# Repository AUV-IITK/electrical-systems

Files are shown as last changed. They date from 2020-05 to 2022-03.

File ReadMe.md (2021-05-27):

**This is the repository for AUV-IITK Electrical subsytem**

Implementing new electrical design with multiple 2layer PCB and more compatible connectors making the electronics modular.
Introducing :
- Power Board for Power Management and routing with fault detection and indicators.
- custom Microcontroller Board
- ESC Breakout boards

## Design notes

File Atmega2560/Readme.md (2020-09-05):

**This is the repository for ATMEGA 2560**

The MicrocontrollerPCB section contains the scematic and the PCB layout done in KICAD and would be updated from time to time.

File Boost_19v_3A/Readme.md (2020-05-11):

# Boost Converter for the NUC

 The simulation has been run on TINA-TI Spice software. Download from here [Link](http://www.ti.com/tool/TINA-TI).

 Results of a simulation on the [Webench](https://webench.ti.com/power-designer/) have been placed in the in the simulation output folder. 

 To run simulation download the schematic and open with TINA-TI.

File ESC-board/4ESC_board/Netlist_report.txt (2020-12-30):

Info: Checking netlist symbol footprint “C1:/5FEA16F4:molex:molex_supersabre_1x2_172043-0201”.

Info: Checking netlist symbol footprint “C2:/5FEA11BD:molex:Molex_Microfit_1x5_436500500”.

Info: Checking netlist symbol footprint “C3:/5FEA0F57:molex:Molex_microfit_2x6_444281201”.

Info: Checking netlist symbol footprint “D1:/5FEA1FA2:Diode_SMD:D_1206_3216Metric_Pad1.42x1.75mm_HandSolder”.

Info: Checking netlist symbol footprint “R1:/5FEA2178:Resistor_SMD:R_1206_3216Metric_Pad1.42x1.75mm_HandSolder”.

Info: Checking netlist symbol footprint “U1:/5FEA0291:ESC:ESC_footprint”.

Info: Checking netlist symbol footprint “U2:/5FEA037F:ESC:ESC_footprint”.

Info: Checking netlist symbol footprint “U3:/5FEA0417:ESC:ESC_footprint”.

Info: Checking netlist symbol footprint “U4:/5FEA04B8:ESC:ESC_footprint”.

Adding new symbol “C1:/5FEA16F4” footprint “molex:molex_supersabre_1x2_172043-0201”.

Changing footprint “C1:/5FEA16F4” pad “2” net name from “” to “/GND”.

Changing footprint “C1:/5FEA16F4” pad “1” net name from “” to “/VIN”.

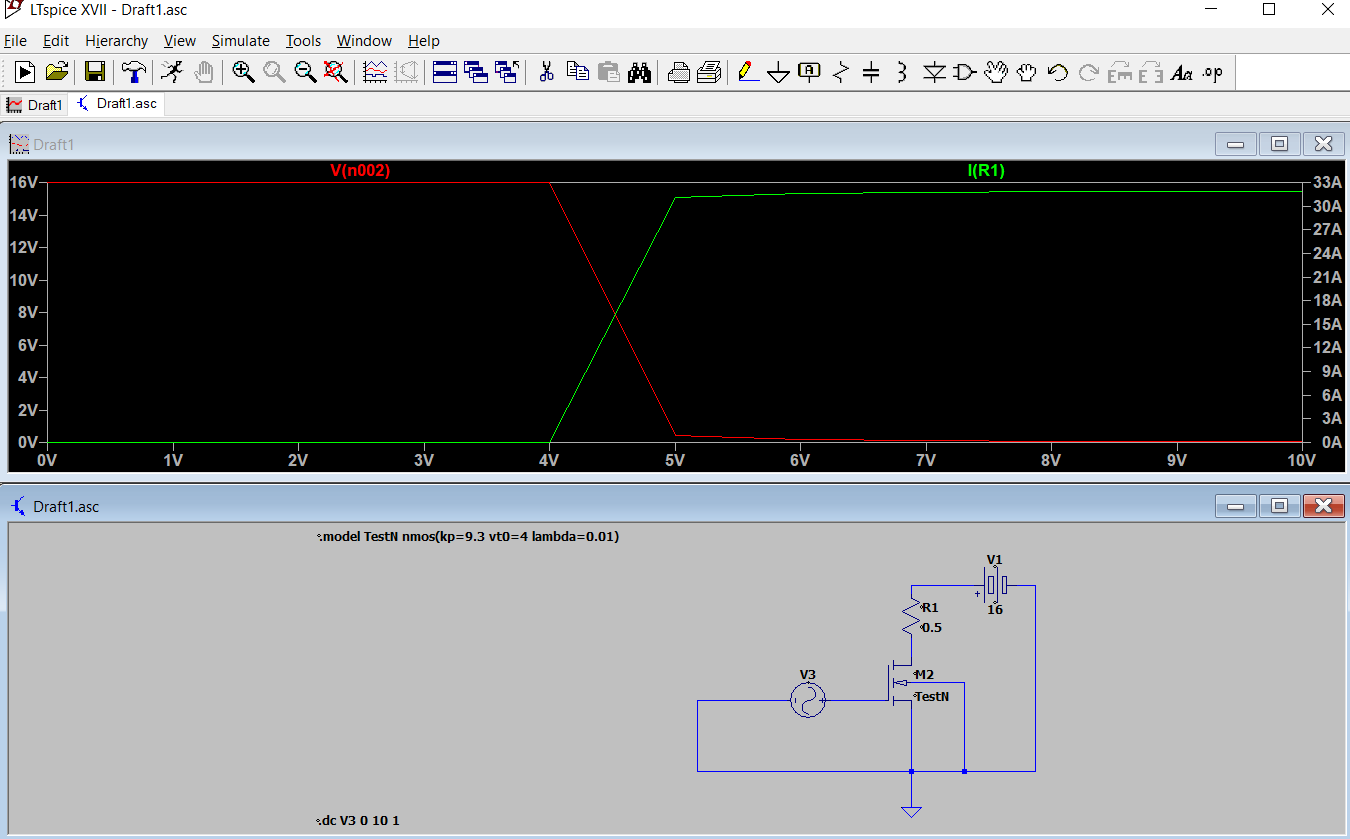
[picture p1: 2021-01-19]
Kill_switch_board/Mosfet/Simulation.png

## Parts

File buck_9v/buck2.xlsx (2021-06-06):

Reference | Value | Price | Mouser Price/Stock | Description | Height | Manufacturer_Name | Manufacturer_Part_Number | Mouser Part Number | Availability | MF | MP | Package | Datasheet
Cvcc1 | 1uF,1mOhm | 12.69 | https://www.mouser.in/ProductDetail/Taiyo-Yuden/TMK212B7105KG-T |  |  |  |  |  |  |  |  |  | ~
Ccomp1 | 18nF,0Ohm | 128.4 | https://www.mouser.in/ProductDetail/KEMET/C1812C183J5GACTU |  |  |  |  |  |  |  |  |  | ~
Cbst1 | 100nF,1mOhm | 7.47 | https://www.mouser.in/ProductDetail/Murata-Electronics/GRM155R71C104KA88D?qs=8YPuuxuUzMJKePo9sU3A2g%3D%3D |  |  |  |  |  |  |  |  |  | ~
Rcomp1 | 2.43kOhm | 7.47 | https://www.mouser.in/ProductDetail/Vishay-Dale/CRCW04022K43FKED?qs=hD42E%2F8yzjrZGhA5WCLdcg%3D%3D |  |  |  |  |  |  |  |  |  | ~
Rpgood1 | 100kOhm | 7.47 | https://www.mouser.in/ProductDetail/Vishay-Dale/CRCW0402100KFKED?qs=OlqPY1CiralZGKRwQ4Glcg%3D%3D |  |  |  |  |  |  |  |  |  | ~
Rs1 | 1.87kOhm | 7.47 | https://www.mouser.in/ProductDetail/Vishay-Dale/CRCW04021K87FKED?qs=YX%252BK5oaHNYoBXdTwHU3ZVw%3D%3D |  |  |  |  |  |  |  |  |  | ~
Rfbb1 | 715Ohm | 7.47 | https://www.mouser.in/ProductDetail/Vishay-Dale/CRCW0402715RFKED?qs=Yor07UEv01XYIyNR0JjcQw%3D%3D |  |  |  |  |  |  |  |  |  | ~
Rfbt1 | 10kOhm | 9.7 | https://www.mouser.in/ProductDetail/Yageo/RC0201FR-0710KL |  |  |  |  |  |  |  |  |  | ~
Ccomp2 | 330pF,0Ohm | 7.47 | https://www.mouser.in/ProductDetail/Murata-Electronics/GRM1555C1H331JA01D?qs=GO3ZKNAOsLOYqN1qv1AduA%3D%3D
Cbyp1 | 2.2uF,1mOhm | 11.2 | https://www.mouser.in/ProductDetail/Taiyo-Yuden/EMK212BJ225KG-T | Multilayer Ceramic Capacitors MLCC - SMD/SMT 2.2uF 16V X5R +/-10% 0805 Gen Purp | 1.35 | TAIYO YUDEN | EMK212BJ225KG-T | 963-EMK212BJ225KG-T |  |  |  |  | https://componentsearchengine.com/Datasheets/1/EMK212BJ225KG-T.pdf
Cout1 | 22uF,1mOhm | 79.13 | https://www.mouser.in/ProductDetail/Taiyo-Yuden/TMK325B7226KMHP | Multilayer Ceramic Capacitors MLCC - SMD/SMT 1210 25V 22uF 10% X7R AEC-Q200 | 2.7 | TAIYO YUDEN | TMK325B7226KMHP | 963-TMK325B7226KMHP |  |  |  |  | https://www.mouser.mx/datasheet/2/396/taiyo_yuden_12132018_mlcc11_hq_e-1510082.pdf
Cout2 | 22uF,1mOhm | 79.13 | https://www.mouser.in/ProductDetail/Taiyo-Yuden/TMK325B7226KMHP | Multilayer Ceramic Capacitors MLCC - SMD/SMT 1210 25V 22uF 10% X7R AEC-Q200 | 2.7 | TAIYO YUDEN | TMK325B7226KMHP | 963-TMK325B7226KMHP |  |  |  |  | https://www.mouser.mx/datasheet/2/396/taiyo_yuden_12132018_mlcc11_hq_e-1510082.pdf
Ccomp3 | 4.7nF,0Ohm | 17.17 | https://www.mouser.in/ProductDetail/TDK/CGA4C2C0G1H472J060AA |  | 0.75 | TDK | CGA4C2C0G1H472J060AA | 810-CGA4C2C0G1H472J |  |  |  |  | https://componentsearchengine.com/Datasheets/1/CGA4C2C0G1H472J060AA.pdf
Rcomp2 | 191Ohm | 7.47 | https://www.mouser.in/ProductDetail/Vishay-Dale/CRCW0402191RFKED?qs=QPqDnsKvzKez8iEW666MbA%3D%3D |  |  |  |  |  |  |  |  |  | ~
M1 | 30V,56Amps | 65.69 | https://www.mouser.in/ProductDetail/Texas-Instruments/CSD17304Q3 | 30V, N ch NexFET MOSFET, single SON3x3, 8.8mOhm |  | Texas Instruments | CSD17304Q3 | 595-CSD17304Q3 |  |  |  |  | http://www.ti.com/lit/gpn/csd17304q3
M2 | 30V,35Amps | 56.73 | https://www.mouser.in/ProductDetail/Texas-Instruments/CSD17577Q3A?qs=m%2F7bTylgptdTq6Yorh0Ysg%3D%3D | 30V, N ch NexFET MOSFET, single SON3x3, 6.4mOhm |  | Texas Instruments | CSD17577Q3A | 595-CSD17577Q3A |  |  |  |  | http://www.ti.com/lit/gpn/csd17577q3a
U1 | TPS40303DRCR | 174.68 | https://www.mouser.in/ProductDetail/Texas-Instruments/TPS40303DRCR?qs=%2Fqzd9s%252BcLd7HFoAWcaijuQ%3D%3D | Switching Controllers 3-20V Wide Input Sync Buck Controller | 1 | Texas Instruments | TPS40303DRCR |  |  |  |  |  | https://www.ti.com/lit/ds/symlink/tps40303.pdf?ts=1621506755531
J1 | 436500400 | 106 | https://www.mouser.in/ProductDetail/Molex/43650-0400
Cin2 | 10uF,1mOhm | 72.41 | https://www.mouser.in/ProductDetail/TDK/C3225X7R1H106M250AC |  |  |  |  |  |  |  |  |  | ~
Cin1 | 10uF,1mOhm | 72.41 | https://www.mouser.in/ProductDetail/TDK/C3225X7R1H106M250AC |  |  |  |  |  |  |  |  |  | ~
L1 | SER2915L-223KL | 350.86 | https://www.mouser.in/ProductDetail/Coilcraft/SER2915L-223KL | Power inductor, high current, 10% tol, SMT, RoHS |  |  |  |  | Unavailable | Coilcraft | SER2915L-223KL | None
Css1 | 3.3nF,1mOhm | 7.47 | https://www.mouser.in/ProductDetail/Murata-Electronics/GRM033R71A332KA01D?qs=AgWb9queBCgkm7%252BKnfrZqA%3D%3D
 |  | 1295.96

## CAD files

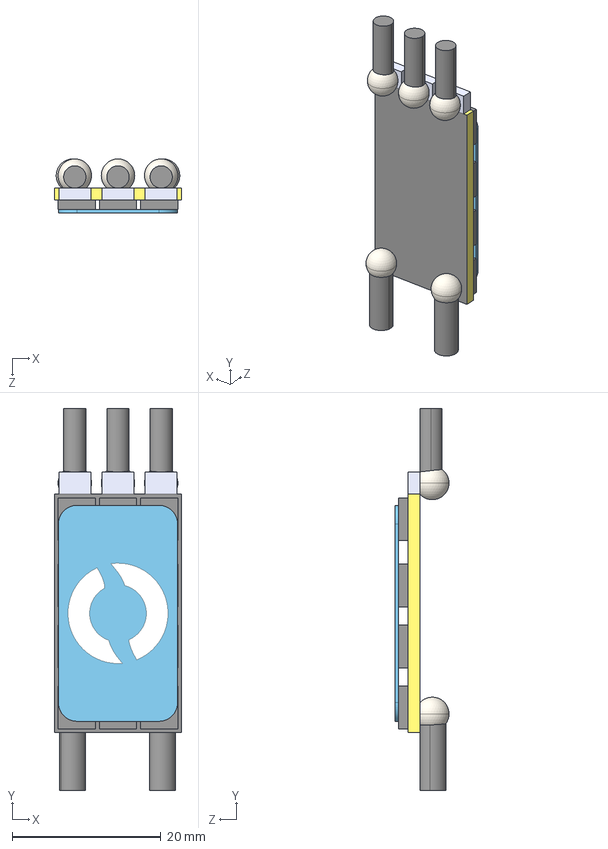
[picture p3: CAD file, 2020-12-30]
ESC-board/3D_models/ESC_BESC30-R3.STEP
17.1 x 51.3 x 7.28 mm
BASICESC-G-PCB-X1
BASICESC-E-MOSFET x 12
BASICESC-M-HEAT-SPREADER-X1
Solder Bead x 5
14AWG Wire x 2
16AWG Wire x 3

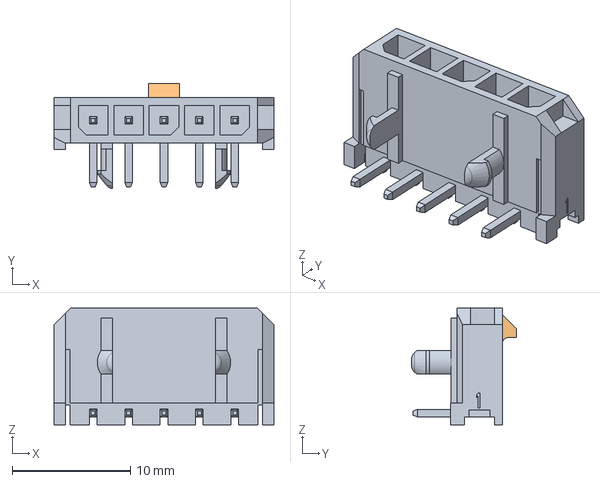
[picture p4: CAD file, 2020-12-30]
ESC-board/3D_models/Molex_Microfit_1x5_436500500.stp
18.6 x 8.91 x 9.90 mm

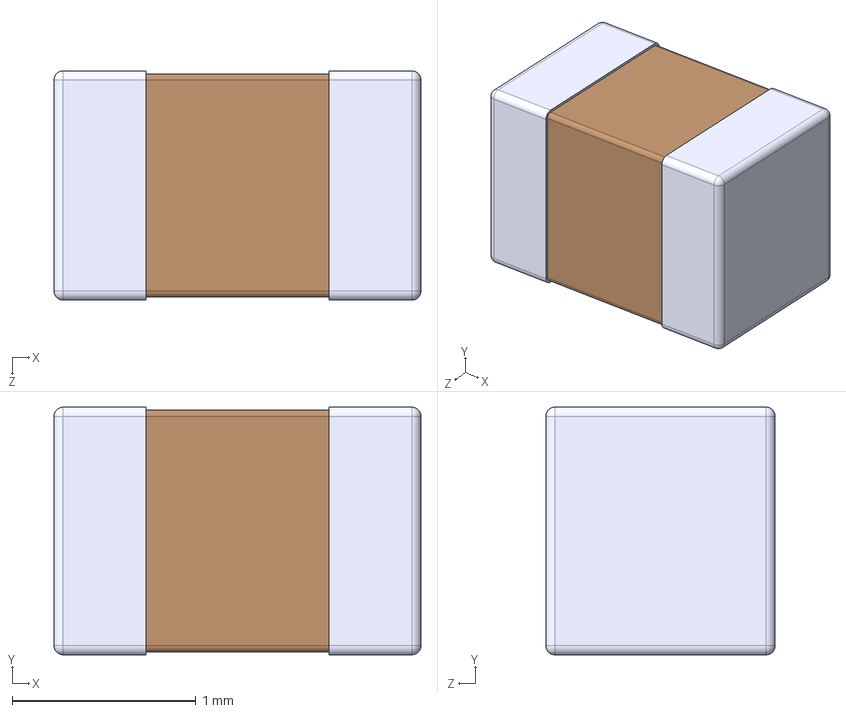
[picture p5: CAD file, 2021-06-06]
buck_9v/BUCK 3d-MODELS/EMK212BJ225KG-T.STEP
2.00 x 1.35 x 1.25 mm

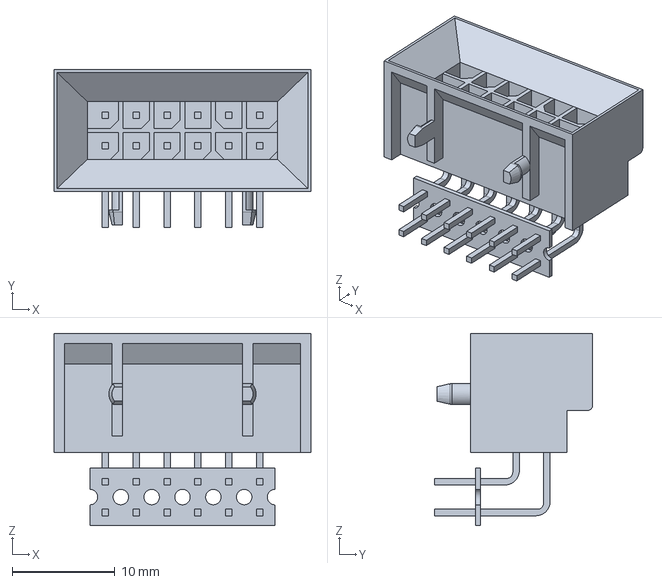
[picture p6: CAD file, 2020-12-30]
ESC-board/3D_models/Molex_microfit_2x6_444281201.stp
25.0 x 15.4 x 18.7 mm

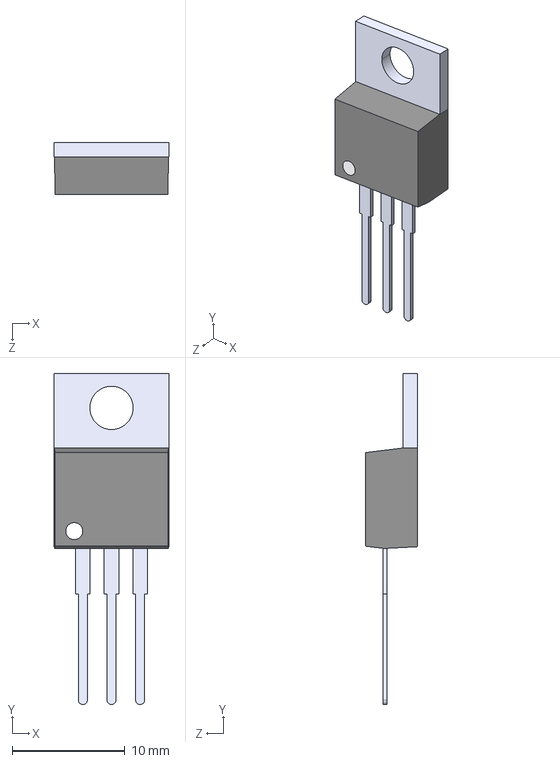
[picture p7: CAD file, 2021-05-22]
Power-Board/3D Model/LM7805CT_NOPB.step
10.2 x 29.3 x 4.57 mm

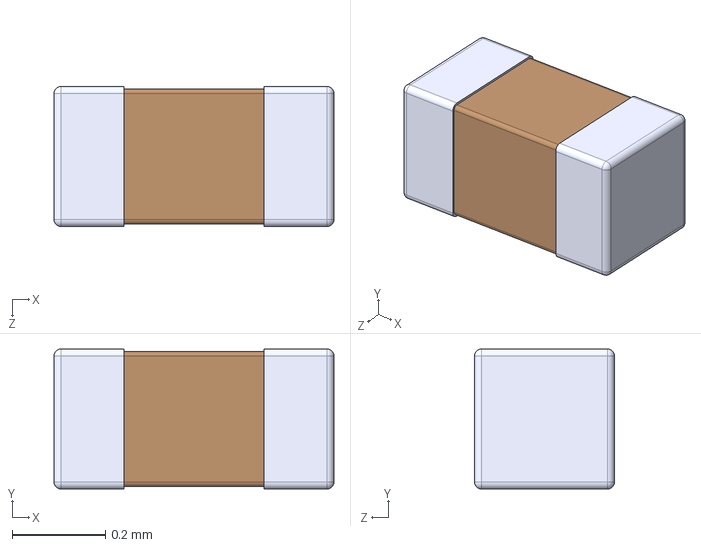
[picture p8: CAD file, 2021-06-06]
buck_9v/BUCK 3d-MODELS/GRM033R71A332KA01D.STEP
0.6 x 0.3 x 0.3 mm

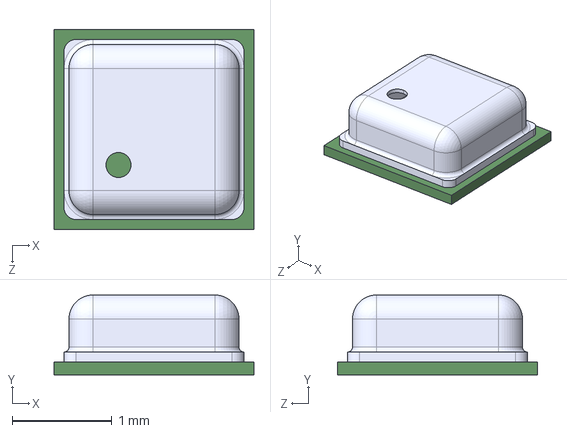
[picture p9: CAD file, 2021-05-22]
Power-Board/3D Model/BMP388.step
2.00 x 0.8 x 2.00 mm

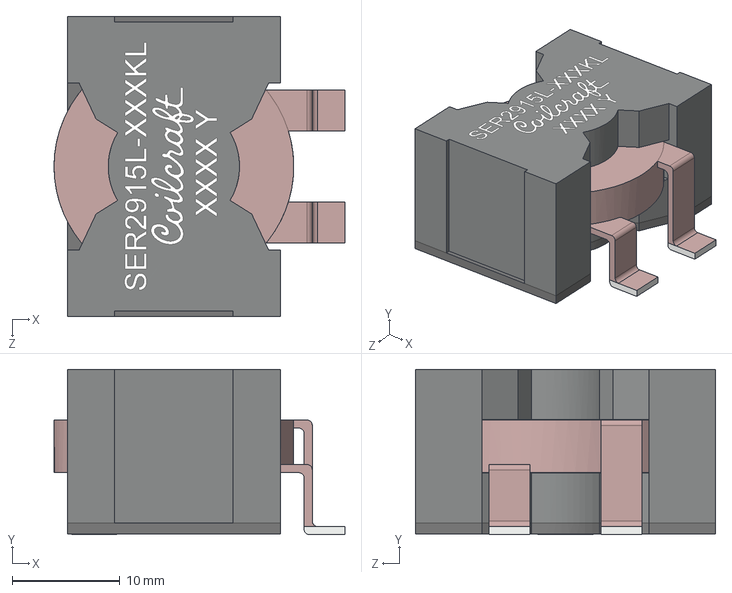
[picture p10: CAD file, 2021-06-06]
buck_9v/BUCK 3d-MODELS/Coilcraft-SER2915L.STEP
27.0 x 15.4 x 27.9 mm

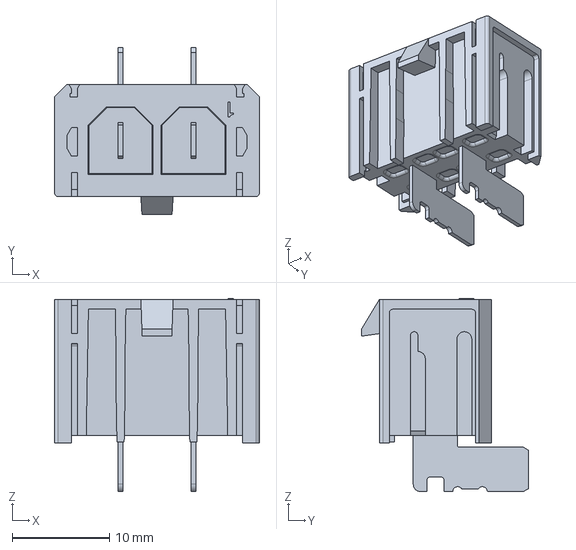
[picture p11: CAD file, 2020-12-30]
Power-Board/3D Model/molex_supersabre_1x2_172043-0201.stp
21.1 x 17.2 x 19.9 mm

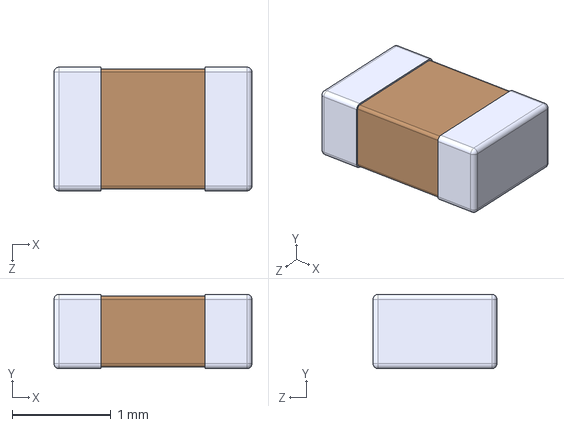
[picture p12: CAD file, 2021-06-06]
buck_9v/BUCK 3d-MODELS/CGA4C2C0G1H472J060AA.STEP
2.00 x 0.75 x 1.25 mm

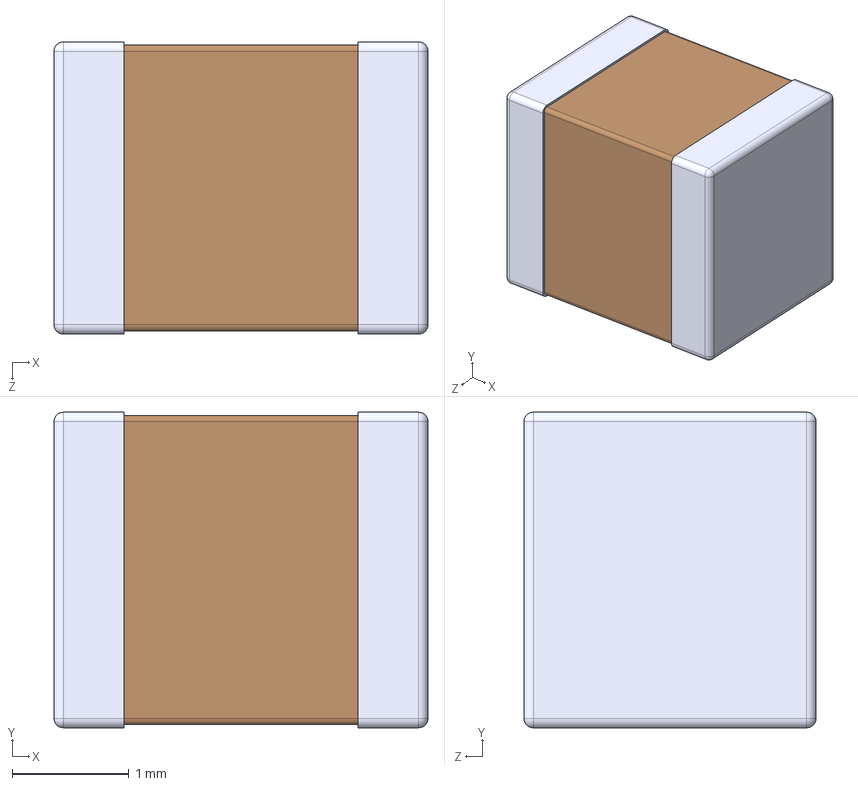
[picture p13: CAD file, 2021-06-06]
buck_9v/BUCK 3d-MODELS/TMK325B7226KMHP.stp
3.20 x 2.70 x 2.50 mm

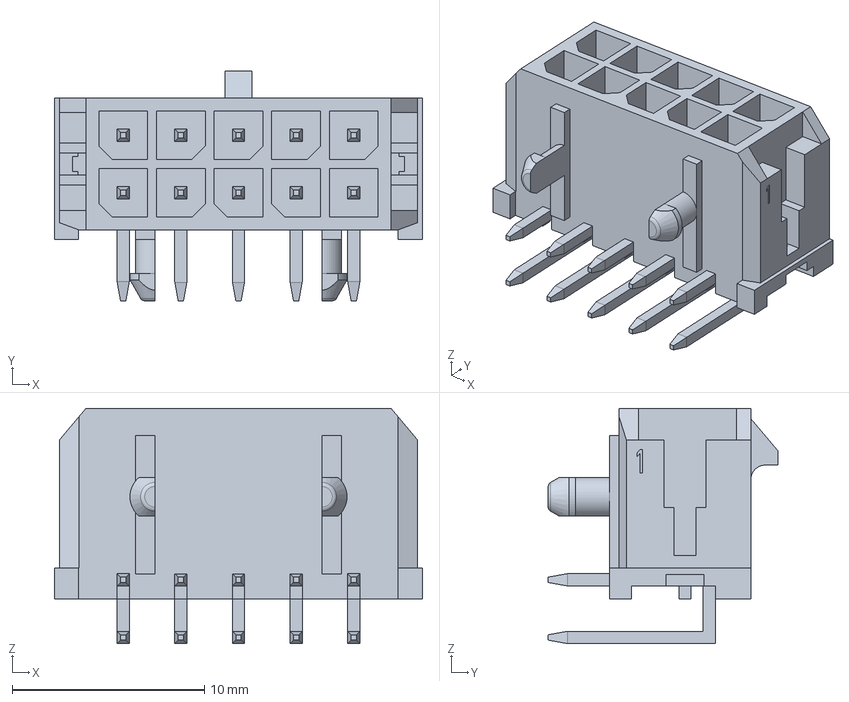
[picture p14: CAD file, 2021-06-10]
Atmega2560/MicrocontrollerPcb/3D model/430451000.stp
19.1 x 12.0 x 12.2 mm

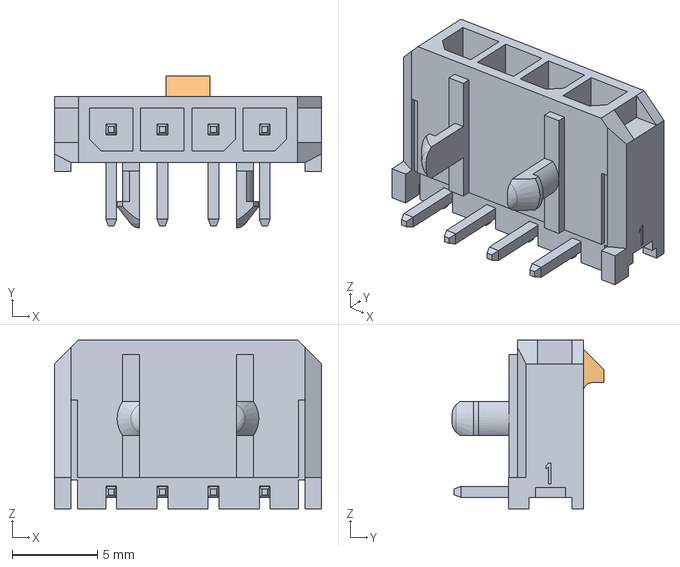
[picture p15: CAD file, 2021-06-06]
buck_9v/BUCK 3d-MODELS/436500400.stp
15.7 x 8.91 x 9.90 mm

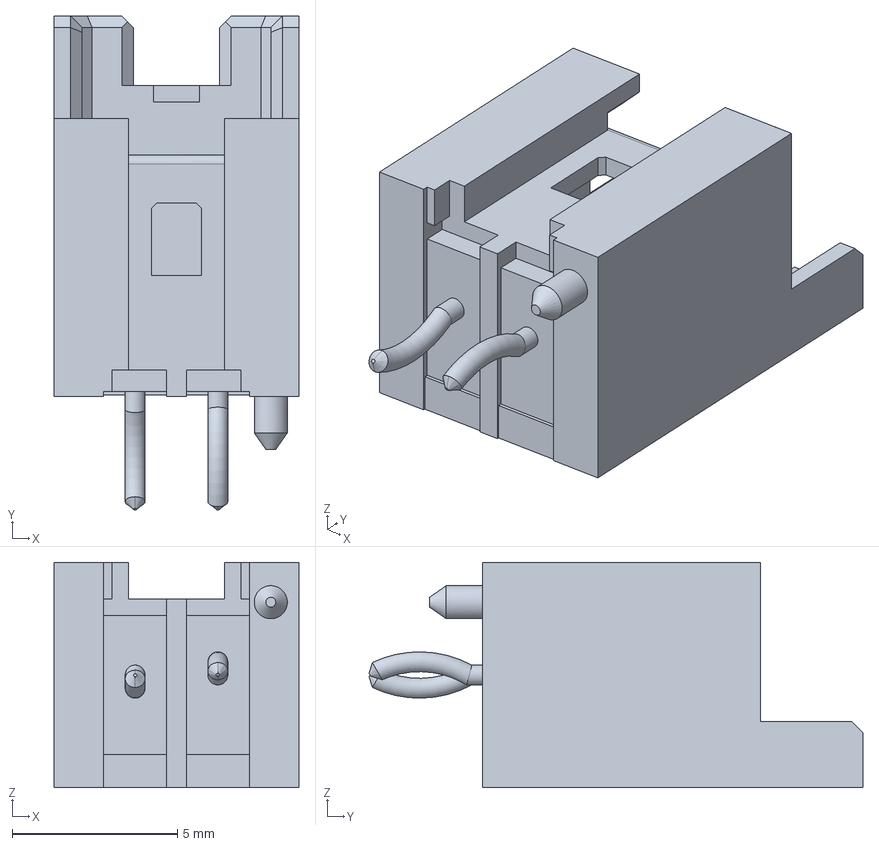
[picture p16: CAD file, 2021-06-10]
Power-Board/3D Model/533750210.stp
7.40 x 14.9 x 6.80 mm

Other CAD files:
Atmega2560/MicrocontrollerPcb/3D model/430450200.stp
buck_9v/BUCK 3d-MODELS/CSD17577Q3A.STEP
Power-Board/3D Model/430450200.stp
Atmega2560/MicrocontrollerPcb/3D model/533750410.stp
Power-Board/3D Model/430450200.stl
Power-Board/3D Model/533750210.stl
buck_9v/BUCK 3d-MODELS/CSD17304Q3.STEP
buck_9v/BUCK 3d-MODELS/TPS40303DRCR.STEP

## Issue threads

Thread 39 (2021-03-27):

Add images for Kicad schematics and PCB layout

Ddevendra, 2021-03-27:
Every time we need to take a look at schematic or PCB we have to open the complete project in KiCad.
So why not just adding 2-3 images of each screen, that would make it easier to check the circuit whenever necessary.

Ddevendra, 2022-03-16:
https://www.pcbway.com/project/OnlineGerberViewer.html

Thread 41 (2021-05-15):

Add I2C logic converter

Ddevendra, 2021-05-15:
add i2c logic level converter circuit for blue robotics pressure sensor
link to i2c level converter module : https://bluerobotics.com/store/comm-control-power/tether-interface/level-converter-r1/

Ddevendra, 2021-08-24:
added

Closed 2021-08-24.

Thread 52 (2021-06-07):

Add polyfuse

Ddevendra, 2021-06-07:
OVER-CURRENT PROTECTION
adding resettable fuse for limiting the current through batteries

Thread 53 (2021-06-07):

correct board outline

Ddevendra, 2021-06-07:
there is some error in board outline
few labels are out of board

neel-singhania, 2022-01-29:
resolved

Closed 2022-08-02.

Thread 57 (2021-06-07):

clear pads from any other layer

Ddevendra, 2021-06-07:
remove the blocking text from pads (text on silk screen layer prints above the pad and creates problem while soldering)

Ddevendra, 2022-03-16:
DONE

Closed 2022-03-16.

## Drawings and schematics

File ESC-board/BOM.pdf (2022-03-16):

3808 | CONNECTORS AND CRIMPS

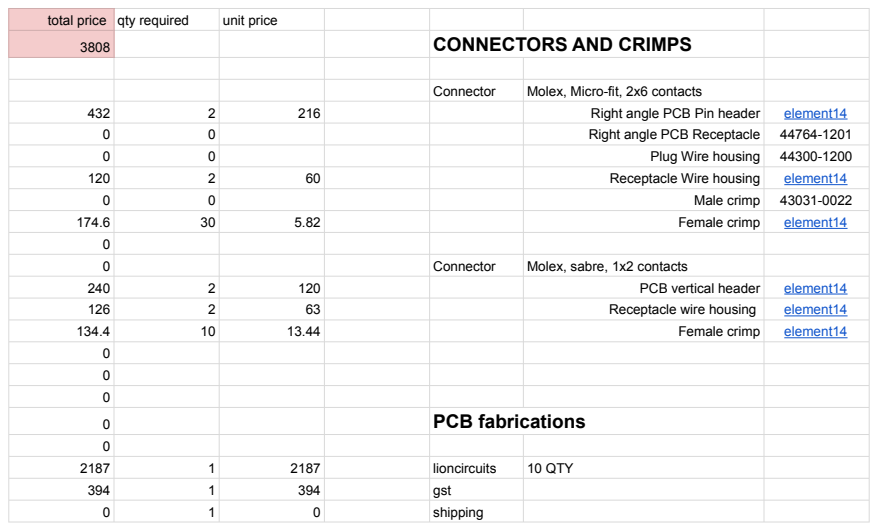
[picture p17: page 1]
total price; qty required; unit price; Connector; Molex, Micro-fit, 2x6 contacts; Right angle PCB Pin header; element14; Right angle PCB Receptacle; Plug Wire housing; Receptacle Wire housing; Male crimp; Female crimp; Molex, sabre, 1x2 contacts; PCB vertical header; Receptacle wire housing; PCB fabrications; lioncircuits; 10 QTY; gst; shipping

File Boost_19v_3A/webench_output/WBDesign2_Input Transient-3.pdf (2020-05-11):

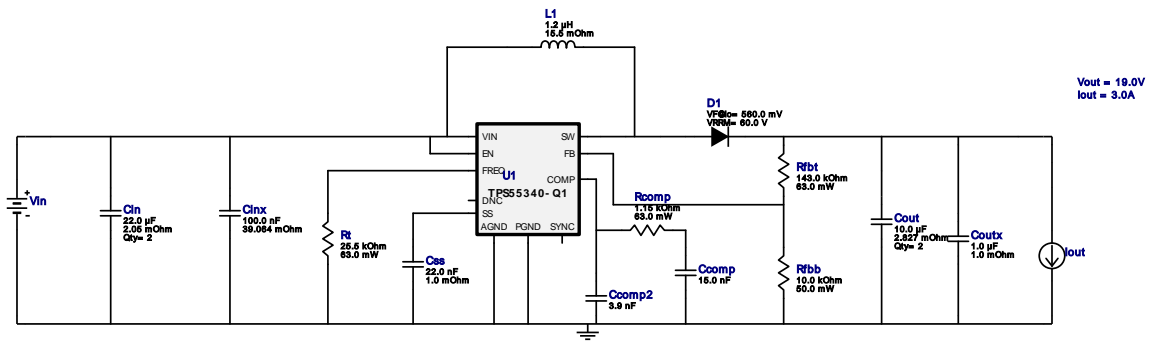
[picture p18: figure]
Cinx 100.0 nF 39.064 mOhm; Css 22.0 nF; 1.0 mOhm; Rfbb; 10.0 kOhm 50.0 mW; Ccomp 15.0 nF Ccomp2; Rt 25.5 kOhm; Cin 22.0 µF 2.05 mOhm Qty= 2; Cout 10.0 µF; 2.827 mOhm Qty= 2; D1 VF@Io= 560.0 mV VRRM= 60.0 V; L1 1.2 µH 15.5 mOhm; Rcomp 1.15 kOhm 63.0 mW; TPS55340- Q1; VIN; AGND; SYNC; COMP; FREQ; PGND; DNC; Rfbt 143.0 kOhm; Vout = 19.0V Iout = 3.0A; Coutx 1.0 µF 1.0 mOhm; Vin; Iout

Copyright © 2020, Texas Instruments Incorporated | 1 | ti.com/webench

WEBENCH®
Design Report TPS55340QRTERQ1 : TPS55340QRTERQ1 14.8V-16.8V to 19.00V @ 3A April 29, 2020 08:47:07 GMT-07:00

## WEBENCH ® Design Report

Design : 2 TPS55340QRTERQ1
TPS55340QRTERQ1 14.8V-16.8V to 19.00V @ 3A

VinMin = 14.8V
VinMax = 16.8V
Vout = 19.0V
Iout = 3.0A

Device = TPS55340QRTERQ1
Topology = Boost
Created = 2020-04-29 08:35:07.948 BOM Cost = $4.90
BOM Count = 16
Total Pd = 2.51W
1. For frequency > 1.6 MHz, the user is required to make sure load current is always greater than "Iout Min" value shown in the Op Vals.

### Design Alerts

Component Selection Information
The TPS55340-Q1 is qualified for Automotive applications. All passives and other components selected in this design may not be qualified for Automotive applications. The user is required to verify that all components in the design meet the qualification and safety requirements for their specific application.

## Electrical BOM

Name | Manufacturer | Part Number | Properties | Qty Price | Footprint
Ccomp | Kemet | C0603C153J3GACTU (http://www.kemet.com/docfinder?Partnumber%3DC0603C153J3GACTU) Series= C0G/NP0 | Cap= 15.0 nF VDC= 25.0 V IRMS= 0.0 A
1 | $0.10
| | | | | 0603 5 mm²
Ccomp2 | TDK | CGJ3E2C0G1H392J080AA (http://product.tdk.com/capacitor/mlcc/en/documents/mlcc%5Fhighreliability%5Fgeneral%5Fen.pdf) Series= C0G/NP0 | Cap= 3.9 nF VDC= 50.0 V IRMS= 0.0 A
1 | $0.07
| | | | | 0603 5 mm²
Cin | TDK | C2012X5R1V226M125AC Series= X5R | Cap= 22.0 uF ESR= 2.05 mOhm VDC= 35.0 V IRMS= 4.5559 A
2 | $0.33
| | | | | 0805 7 mm²
Cinx | TDK | CGA2B3X7R1H104K050BB (https://product.tdk.com/en/search/capacitor/ceramic/mlcc/info?part%5Fno%3DCGA2B3X7R1H104K050BB) Series= X7R

Cap= 100.0 nF
ESR= 39.064 mOhm
VDC= 50.0 V
IRMS= 814.67 mA

1 $0.02
0402 3 mm²
Cout | TDK | CGA6P3X7S1H106K250AB (https://product.tdk.com/en/search/capacitor/ceramic/mlcc/info?part%5Fno%3DCGA6P3X7S1H106K250AB) Series= X7S

Cap= 10.0 uF
ESR= 2.827 mOhm
VDC= 50.0 V
IRMS= 4.3729 A

2 $0.33
1210_280 15 mm²
Coutx | Taiyo Yuden | GMK212B7105KG-T (http://www.yuden.co.jp/ut/product/pdf/djmk%5Fe.pdf) Series= X7R

Cap= 1.0 uF
ESR= 1.0 mOhm
VDC= 35.0 V
IRMS= 0.0 A

1 $0.03
0805 7 mm²
Css | MuRata | GRM155R71C223KA01D (http://search.murata.co.jp/Ceramy/PnsearchViewAction.do) Series= X7R

Cap= 22.0 nF
ESR= 1.0 mOhm
VDC= 16.0 V
IRMS= 0.0 A

1 $0.01
0402 3 mm²
D1 | Diodes Inc. | PDS760-13 | VF@Io= 560.0 mV VRRM= 60.0 V
1 | $0.63

PowerDI5 50 mm²
L1 | Wurth Elektronik | 74438357012 (http://katalog.we%2Donline.de/pbs/datasheet/74438357012.pdf) | L= 1.2 µH 15.5 mOhm
1 | $1.14
WE-MAPI_4030 26 mm²

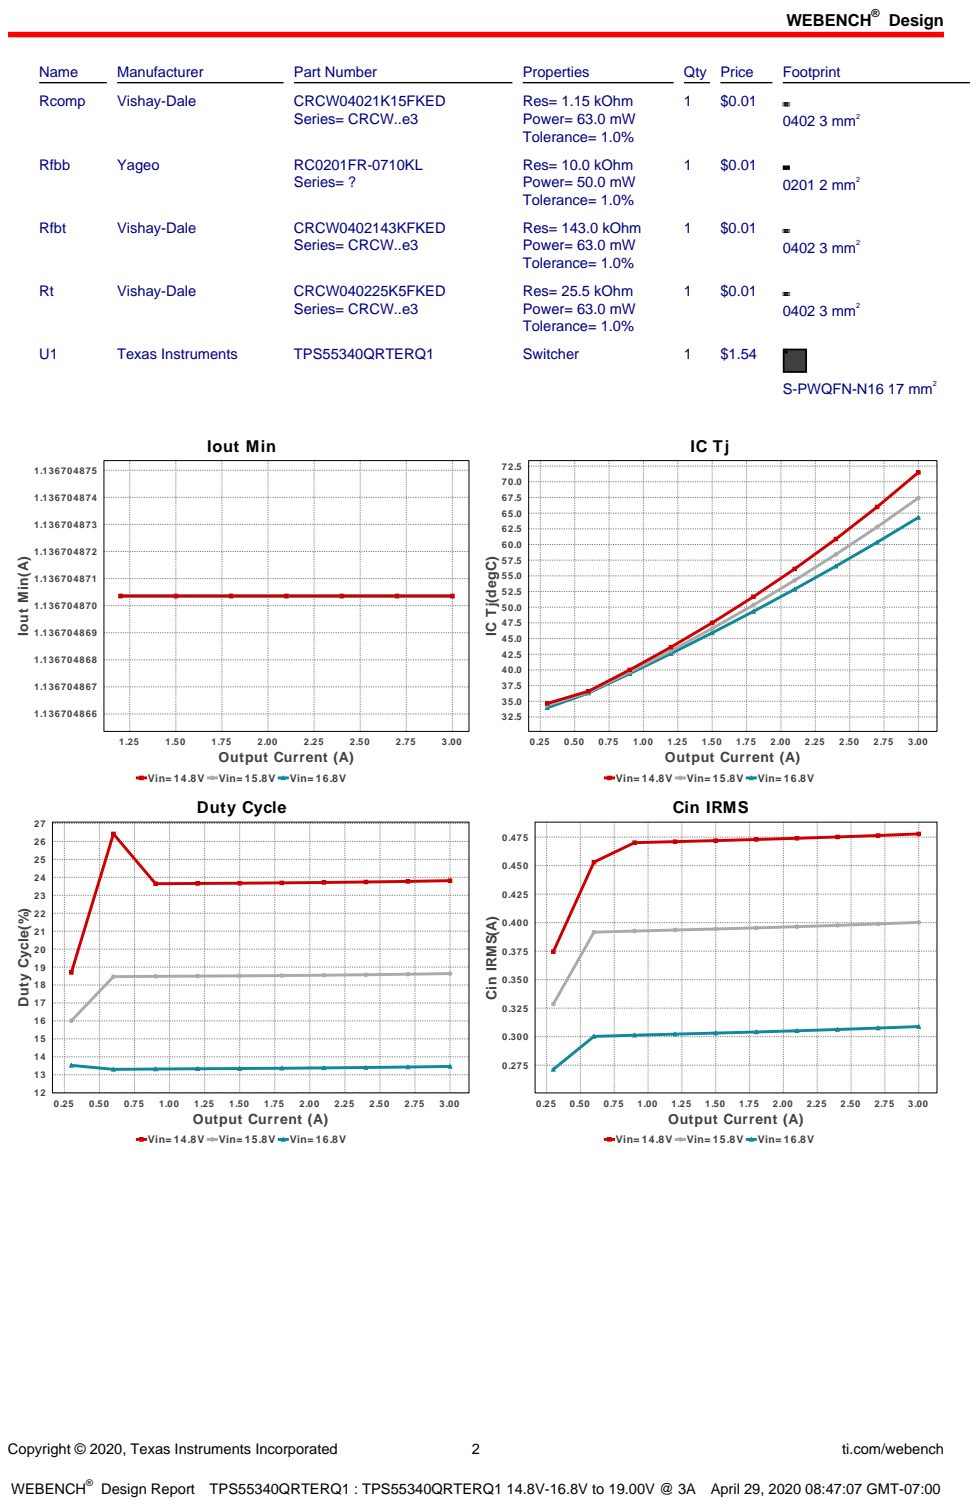
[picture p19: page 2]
Design; Copyright © 2020, Texas Instruments Incorporated; ti.com/webench; Name; Manufacturer; Part Number; Properties; Qty Price; Footprint; Rcomp; Vishay-Dale; CRCW04021K15FKED; Series= CRCW..e3; Res= 1.15 kOhm Power= 63.0 mW Tolerance= 1.0%; 0402 3 mm²; Rfbb; Yageo; Series= ?; Res= 10.0 kOhm Power= 50.0 mW Tolerance= 1.0%; 0201 2 mm²; Rfbt; CRCW0402143KFKED; Res= 143.0 kOhm Power= 63.0 mW Tolerance= 1.0%; CRCW040225K5FKED; Res= 25.5 kOhm Power= 63.0 mW Tolerance= 1.0%; Texas Instruments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

IC Tj(degC)

Vin= 14.8V Vin= 15.8V Vin= 16.8V
Duty Cycle

Cin IRMS

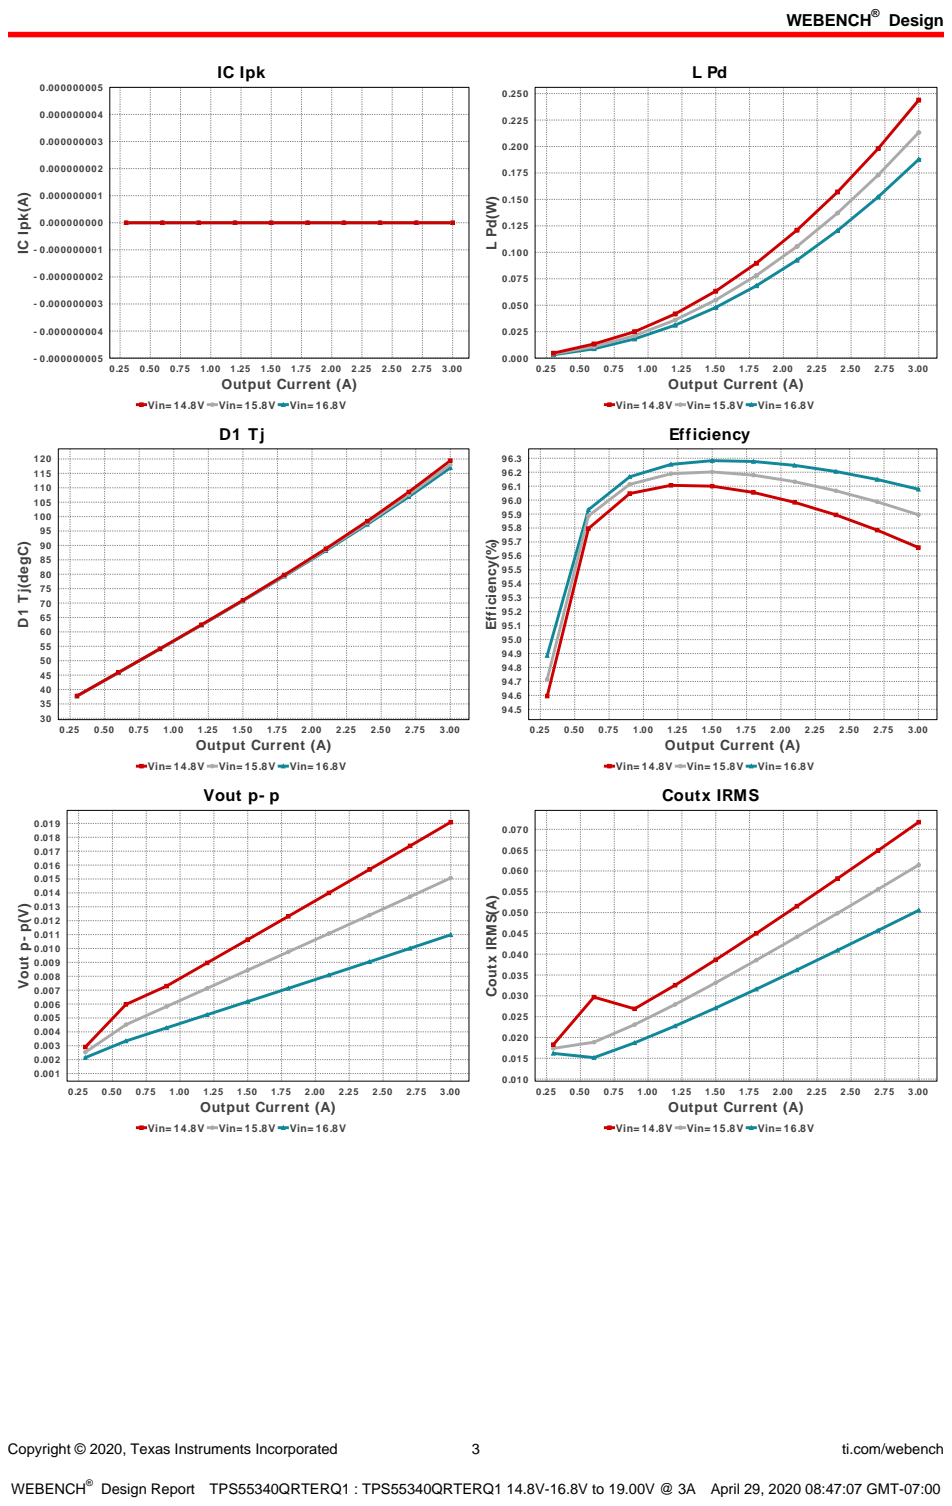
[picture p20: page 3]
Copyright © 2020, Texas Instruments Incorporated; ti.com/webench; IC Ipk; 0.25 0.50 0.75 1.00 1.25 1.50 1.75 2.00 2.25 2.50 2.75 3.00 Output Current (A); IC Ipk(A); 3.00 Output Current (A); D1 Tj(degC); Efficiency(%); Vout p- p(V); Coutx IRMS(A)

Vin= 14.8V Vin= 15.8V Vin= 16.8V

Efficiency

Vout p- p

Coutx IRMS

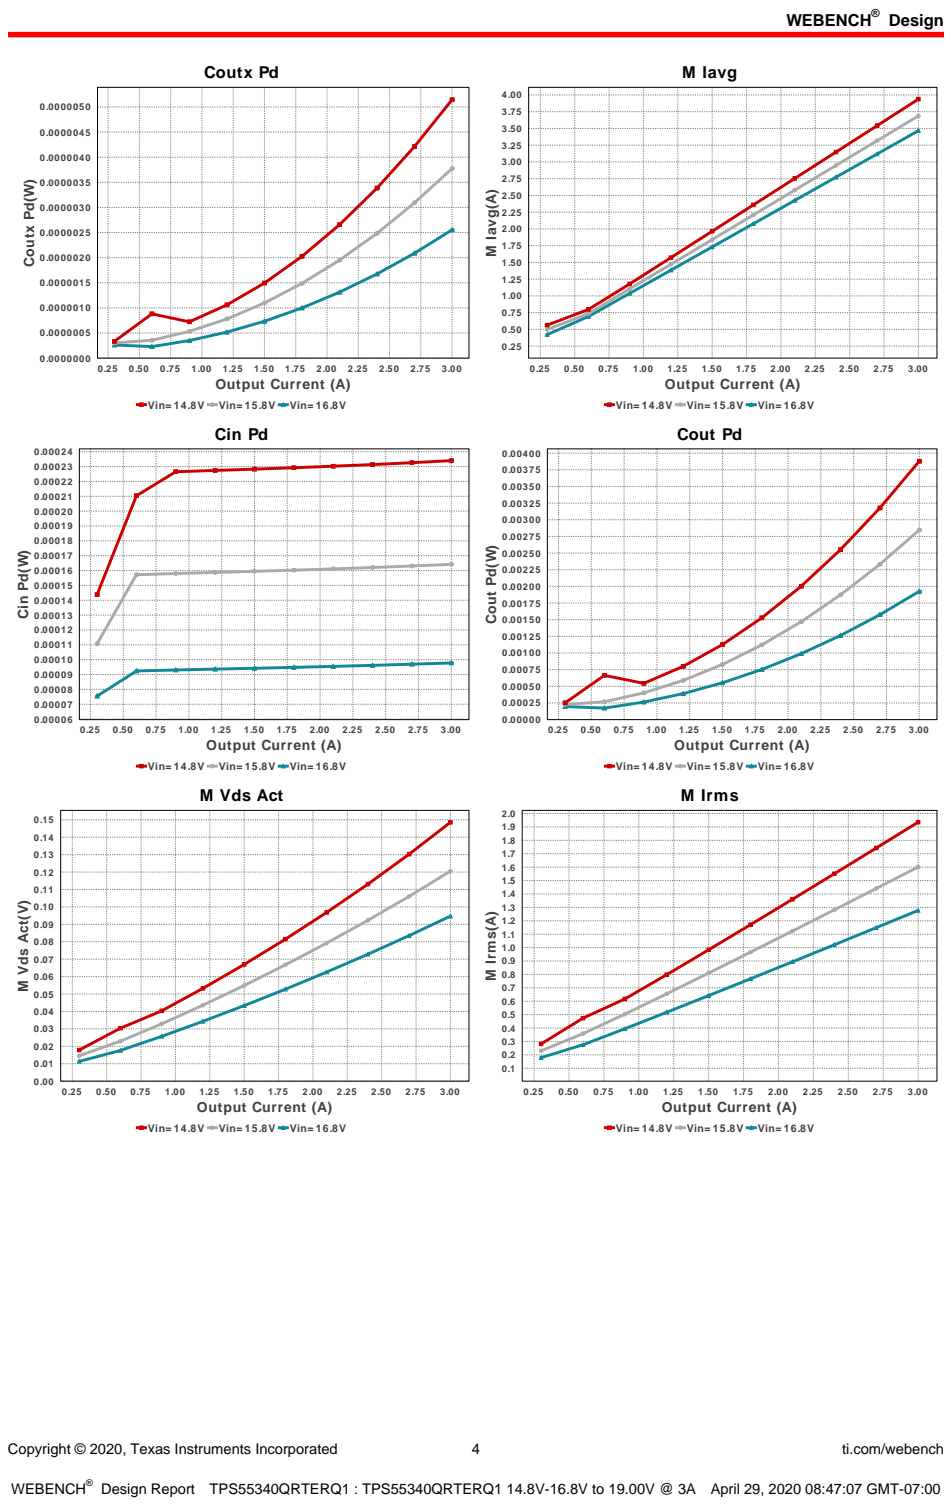
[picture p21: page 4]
Copyright © 2020, Texas Instruments Incorporated; ti.com/webench; Coutx Pd; 0.25 0.50 0.75 1.00 1.25 1.50 1.75 2.00 2.25 2.50 2.75 3.00 Output Current (A); Coutx Pd(W); M Iavg; 3.00 Output Current (A); M Iavg(A); Cin Pd; Cin Pd(W); Cout Pd; Cout Pd(W); M Vds Act(V); M Irms; M Irms(A)

Vin= 14.8V Vin= 15.8V Vin= 16.8V

M Vds Act
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

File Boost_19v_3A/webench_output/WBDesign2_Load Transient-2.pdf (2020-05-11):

Cinx 100.0 nF 39.064 mOhm; Css 22.0 nF; 1.0 mOhm; Rfbb; 10.0 kOhm 50.0 mW; Ccomp 15.0 nF Ccomp2; Rt 25.5 kOhm; Cin 22.0 µF 2.05 mOhm Qty= 2; Cout 10.0 µF; 2.827 mOhm Qty= 2; D1 VF@Io= 560.0 mV VRRM= 60.0 V; L1 1.2 µH 15.5 mOhm; Rcomp 1.15 kOhm 63.0 mW; TPS55340- Q1; VIN; AGND; SYNC; COMP; FREQ; PGND; DNC; Rfbt 143.0 kOhm; Vout = 19.0V Iout = 3.0A; Coutx 1.0 µF 1.0 mOhm; Vin; Iout

Copyright © 2020, Texas Instruments Incorporated | 1 | ti.com/webench

WEBENCH®
Design Report TPS55340QRTERQ1 : TPS55340QRTERQ1 14.8V-16.8V to 19.00V @ 3A April 29, 2020 08:43:38 GMT-07:00

## WEBENCH ® Design Report

Design : 2 TPS55340QRTERQ1
TPS55340QRTERQ1 14.8V-16.8V to 19.00V @ 3A

VinMin = 14.8V
VinMax = 16.8V
Vout = 19.0V
Iout = 3.0A

Device = TPS55340QRTERQ1
Topology = Boost
Created = 2020-04-29 08:35:07.948 BOM Cost = $4.90
BOM Count = 16
Total Pd = 2.51W
1. For frequency > 1.6 MHz, the user is required to make sure load current is always greater than "Iout Min" value shown in the Op Vals.

### Design Alerts

Component Selection Information
The TPS55340-Q1 is qualified for Automotive applications. All passives and other components selected in this design may not be qualified for Automotive applications. The user is required to verify that all components in the design meet the qualification and safety requirements for their specific application.

## Electrical BOM

Name | Manufacturer | Part Number | Properties | Qty Price | Footprint
Ccomp | Kemet | C0603C153J3GACTU (http://www.kemet.com/docfinder?Partnumber%3DC0603C153J3GACTU) Series= C0G/NP0 | Cap= 15.0 nF VDC= 25.0 V IRMS= 0.0 A
1 | $0.10
| | | | | 0603 5 mm²
Ccomp2 | TDK | CGJ3E2C0G1H392J080AA (http://product.tdk.com/capacitor/mlcc/en/documents/mlcc%5Fhighreliability%5Fgeneral%5Fen.pdf) Series= C0G/NP0 | Cap= 3.9 nF VDC= 50.0 V IRMS= 0.0 A
1 | $0.07
| | | | | 0603 5 mm²
Cin | TDK | C2012X5R1V226M125AC Series= X5R | Cap= 22.0 uF ESR= 2.05 mOhm VDC= 35.0 V IRMS= 4.5559 A
2 | $0.33
| | | | | 0805 7 mm²
Cinx | TDK | CGA2B3X7R1H104K050BB (https://product.tdk.com/en/search/capacitor/ceramic/mlcc/info?part%5Fno%3DCGA2B3X7R1H104K050BB) Series= X7R

Cap= 100.0 nF
ESR= 39.064 mOhm
VDC= 50.0 V
IRMS= 814.67 mA

1 $0.02
0402 3 mm²
Cout | TDK | CGA6P3X7S1H106K250AB (https://product.tdk.com/en/search/capacitor/ceramic/mlcc/info?part%5Fno%3DCGA6P3X7S1H106K250AB) Series= X7S

Cap= 10.0 uF
ESR= 2.827 mOhm
VDC= 50.0 V
IRMS= 4.3729 A

2 $0.33
1210_280 15 mm²
Coutx | Taiyo Yuden | GMK212B7105KG-T (http://www.yuden.co.jp/ut/product/pdf/djmk%5Fe.pdf) Series= X7R

Cap= 1.0 uF
ESR= 1.0 mOhm
VDC= 35.0 V
IRMS= 0.0 A

1 $0.03
0805 7 mm²
Css | MuRata | GRM155R71C223KA01D (http://search.murata.co.jp/Ceramy/PnsearchViewAction.do) Series= X7R

Cap= 22.0 nF
ESR= 1.0 mOhm
VDC= 16.0 V
IRMS= 0.0 A

1 $0.01
0402 3 mm²
D1 | Diodes Inc. | PDS760-13 | VF@Io= 560.0 mV VRRM= 60.0 V
1 | $0.63

PowerDI5 50 mm²
L1 | Wurth Elektronik | 74438357012 (http://katalog.we%2Donline.de/pbs/datasheet/74438357012.pdf) | L= 1.2 µH 15.5 mOhm
1 | $1.14
WE-MAPI_4030 26 mm²

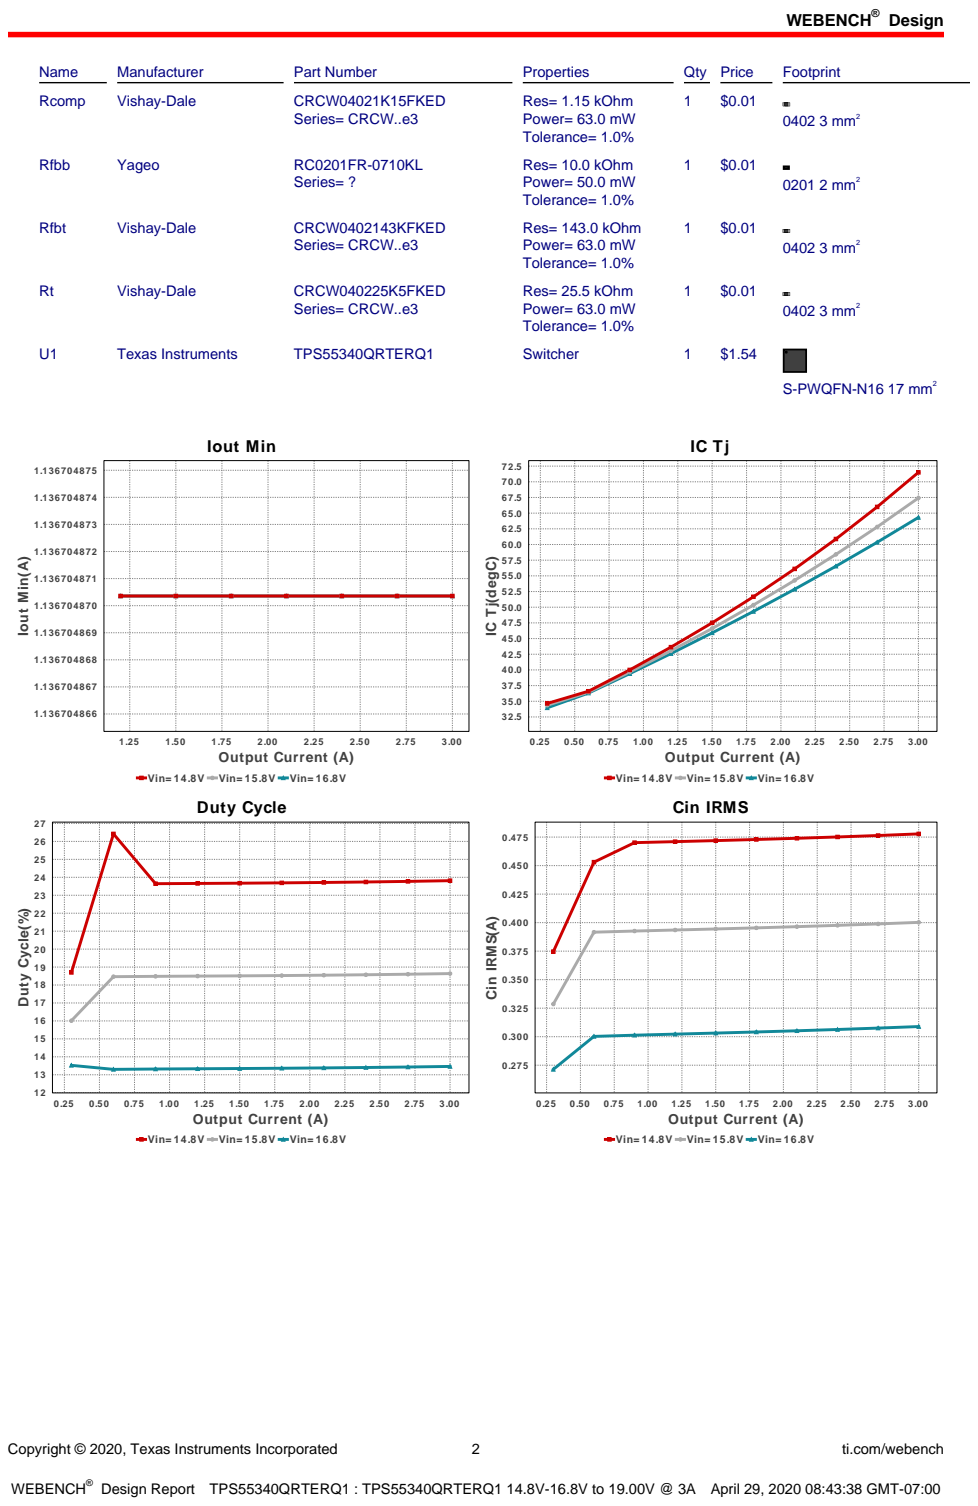
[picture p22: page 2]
Design; Copyright © 2020, Texas Instruments Incorporated; ti.com/webench; Name; Manufacturer; Part Number; Properties; Qty Price; Footprint; Rcomp; Vishay-Dale; CRCW04021K15FKED; Series= CRCW..e3; Res= 1.15 kOhm Power= 63.0 mW Tolerance= 1.0%; 0402 3 mm²; Rfbb; Yageo; Series= ?; Res= 10.0 kOhm Power= 50.0 mW Tolerance= 1.0%; 0201 2 mm²; Rfbt; CRCW0402143KFKED; Res= 143.0 kOhm Power= 63.0 mW Tolerance= 1.0%; CRCW040225K5FKED; Res= 25.5 kOhm Power= 63.0 mW Tolerance= 1.0%; Texas Instruments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

IC Tj(degC)

Vin= 14.8V Vin= 15.8V Vin= 16.8V
Duty Cycle

Cin IRMS

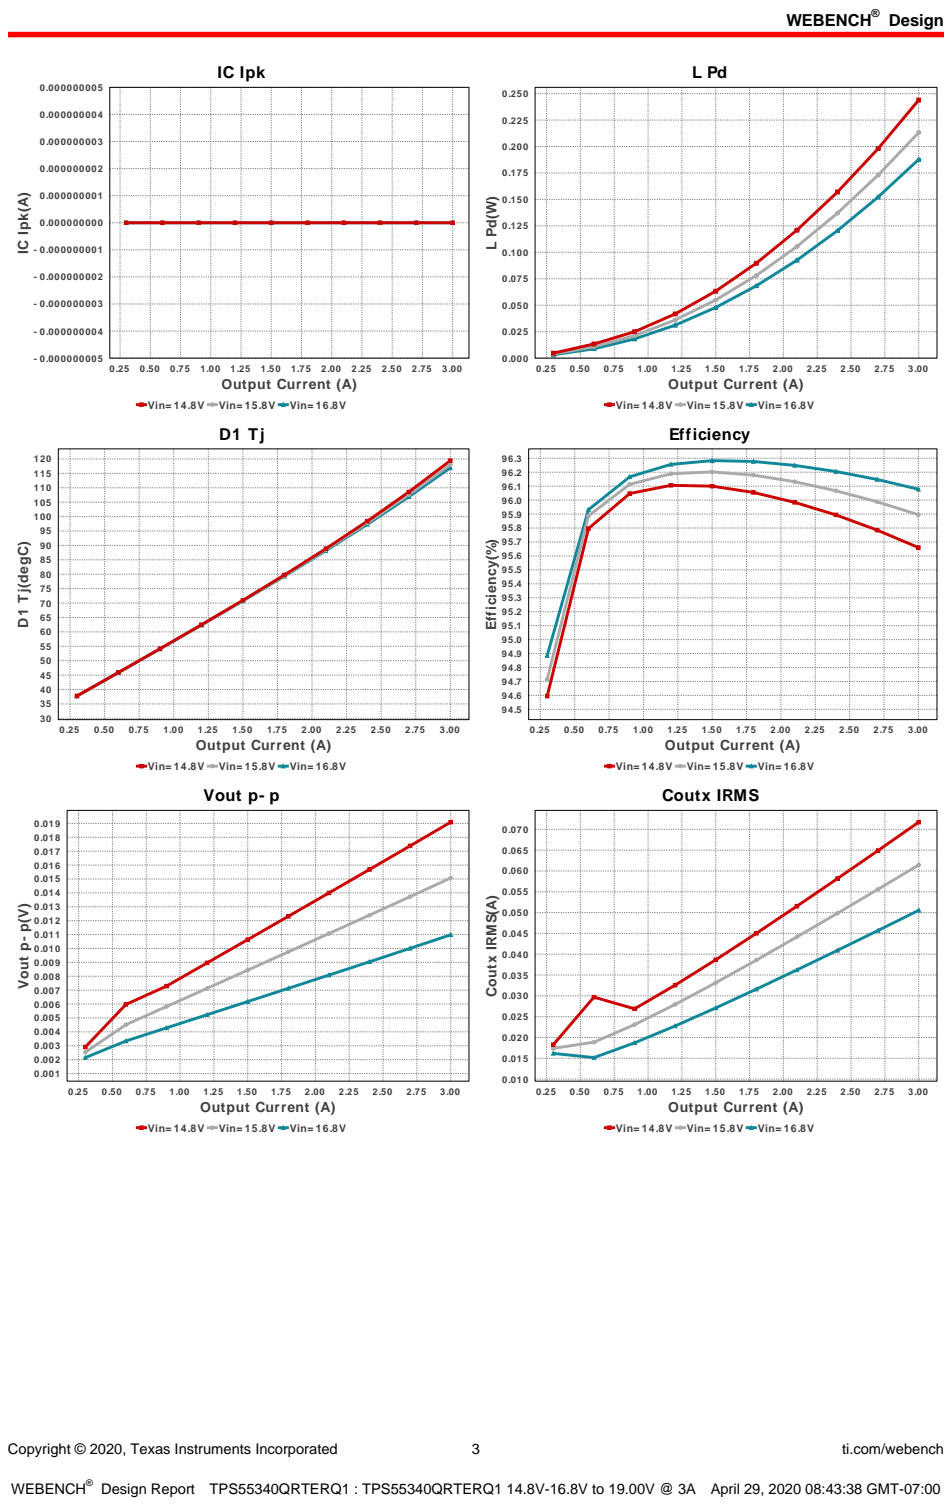
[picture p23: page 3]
Copyright © 2020, Texas Instruments Incorporated; ti.com/webench; IC Ipk; 0.25 0.50 0.75 1.00 1.25 1.50 1.75 2.00 2.25 2.50 2.75 3.00 Output Current (A); IC Ipk(A); 3.00 Output Current (A); D1 Tj(degC); Efficiency(%); Vout p- p(V); Coutx IRMS(A)

Vin= 14.8V Vin= 15.8V Vin= 16.8V

Efficiency

Vout p- p

Coutx IRMS

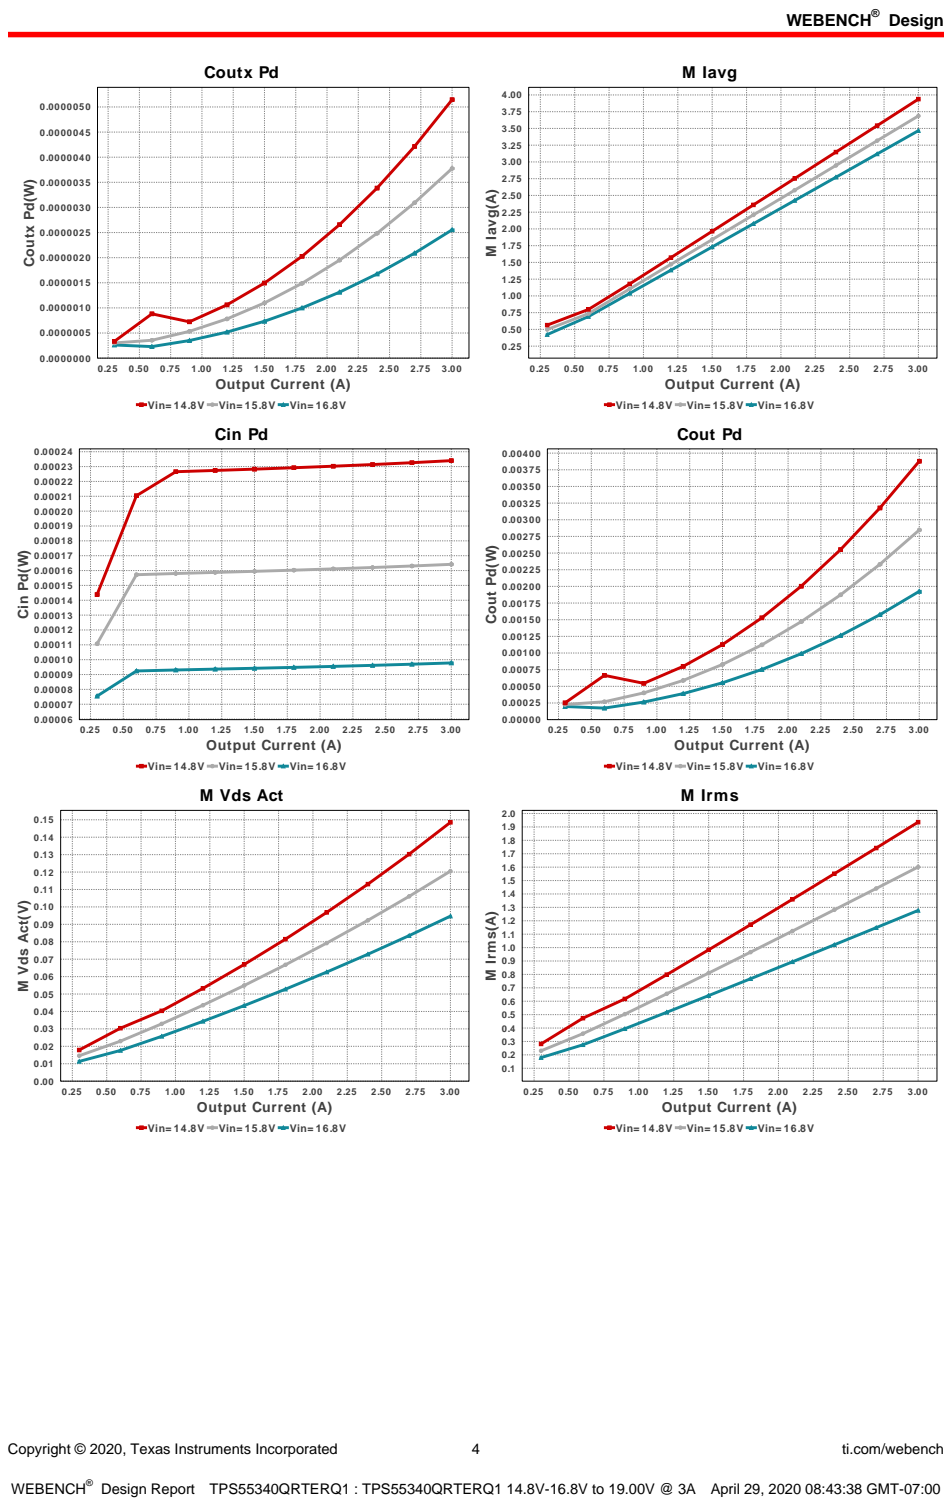
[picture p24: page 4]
Copyright © 2020, Texas Instruments Incorporated; ti.com/webench; Coutx Pd; 0.25 0.50 0.75 1.00 1.25 1.50 1.75 2.00 2.25 2.50 2.75 3.00 Output Current (A); Coutx Pd(W); M Iavg; 3.00 Output Current (A); M Iavg(A); Cin Pd; Cin Pd(W); Cout Pd; Cout Pd(W); M Vds Act(V); M Irms; M Irms(A)

Vin= 14.8V Vin= 15.8V Vin= 16.8V

M Vds Act
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

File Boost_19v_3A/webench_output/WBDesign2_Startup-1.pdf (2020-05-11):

Cinx 100.0 nF 39.064 mOhm; Css 22.0 nF; 1.0 mOhm; Rfbb; 10.0 kOhm 50.0 mW; Ccomp 15.0 nF Ccomp2; Rt 25.5 kOhm; Cin 22.0 µF 2.05 mOhm Qty= 2; Cout 10.0 µF; 2.827 mOhm Qty= 2; D1 VF@Io= 560.0 mV VRRM= 60.0 V; L1 1.2 µH 15.5 mOhm; Rcomp 1.15 kOhm 63.0 mW; TPS55340- Q1; VIN; AGND; SYNC; COMP; FREQ; PGND; DNC; Rfbt 143.0 kOhm; Vout = 19.0V Iout = 3.0A; Coutx 1.0 µF 1.0 mOhm; Vin; Iout

Copyright © 2020, Texas Instruments Incorporated | 1 | ti.com/webench

WEBENCH®
Design Report TPS55340QRTERQ1 : TPS55340QRTERQ1 14.8V-16.8V to 19.00V @ 3A April 29, 2020 08:43:23 GMT-07:00

## WEBENCH ® Design Report

Design : 2 TPS55340QRTERQ1
TPS55340QRTERQ1 14.8V-16.8V to 19.00V @ 3A

VinMin = 14.8V
VinMax = 16.8V
Vout = 19.0V
Iout = 3.0A

Device = TPS55340QRTERQ1
Topology = Boost
Created = 2020-04-29 08:35:07.948 BOM Cost = $4.90
BOM Count = 16
Total Pd = 2.51W
1. For frequency > 1.6 MHz, the user is required to make sure load current is always greater than "Iout Min" value shown in the Op Vals.

### Design Alerts

Component Selection Information
The TPS55340-Q1 is qualified for Automotive applications. All passives and other components selected in this design may not be qualified for Automotive applications. The user is required to verify that all components in the design meet the qualification and safety requirements for their specific application.

## Electrical BOM

Name | Manufacturer | Part Number | Properties | Qty Price | Footprint
Ccomp | Kemet | C0603C153J3GACTU (http://www.kemet.com/docfinder?Partnumber%3DC0603C153J3GACTU) Series= C0G/NP0 | Cap= 15.0 nF VDC= 25.0 V IRMS= 0.0 A
1 | $0.10
| | | | | 0603 5 mm²
Ccomp2 | TDK | CGJ3E2C0G1H392J080AA (http://product.tdk.com/capacitor/mlcc/en/documents/mlcc%5Fhighreliability%5Fgeneral%5Fen.pdf) Series= C0G/NP0 | Cap= 3.9 nF VDC= 50.0 V IRMS= 0.0 A
1 | $0.07
| | | | | 0603 5 mm²
Cin | TDK | C2012X5R1V226M125AC Series= X5R | Cap= 22.0 uF ESR= 2.05 mOhm VDC= 35.0 V IRMS= 4.5559 A
2 | $0.33
| | | | | 0805 7 mm²
Cinx | TDK | CGA2B3X7R1H104K050BB (https://product.tdk.com/en/search/capacitor/ceramic/mlcc/info?part%5Fno%3DCGA2B3X7R1H104K050BB) Series= X7R

Cap= 100.0 nF
ESR= 39.064 mOhm
VDC= 50.0 V
IRMS= 814.67 mA

1 $0.02
0402 3 mm²
Cout | TDK | CGA6P3X7S1H106K250AB (https://product.tdk.com/en/search/capacitor/ceramic/mlcc/info?part%5Fno%3DCGA6P3X7S1H106K250AB) Series= X7S

Cap= 10.0 uF
ESR= 2.827 mOhm
VDC= 50.0 V
IRMS= 4.3729 A

2 $0.33
1210_280 15 mm²
Coutx | Taiyo Yuden | GMK212B7105KG-T (http://www.yuden.co.jp/ut/product/pdf/djmk%5Fe.pdf) Series= X7R

Cap= 1.0 uF
ESR= 1.0 mOhm
VDC= 35.0 V
IRMS= 0.0 A

1 $0.03
0805 7 mm²
Css | MuRata | GRM155R71C223KA01D (http://search.murata.co.jp/Ceramy/PnsearchViewAction.do) Series= X7R

Cap= 22.0 nF
ESR= 1.0 mOhm
VDC= 16.0 V
IRMS= 0.0 A

1 $0.01
0402 3 mm²
D1 | Diodes Inc. | PDS760-13 | VF@Io= 560.0 mV VRRM= 60.0 V
1 | $0.63

PowerDI5 50 mm²
L1 | Wurth Elektronik | 74438357012 (http://katalog.we%2Donline.de/pbs/datasheet/74438357012.pdf) | L= 1.2 µH 15.5 mOhm
1 | $1.14
WE-MAPI_4030 26 mm²

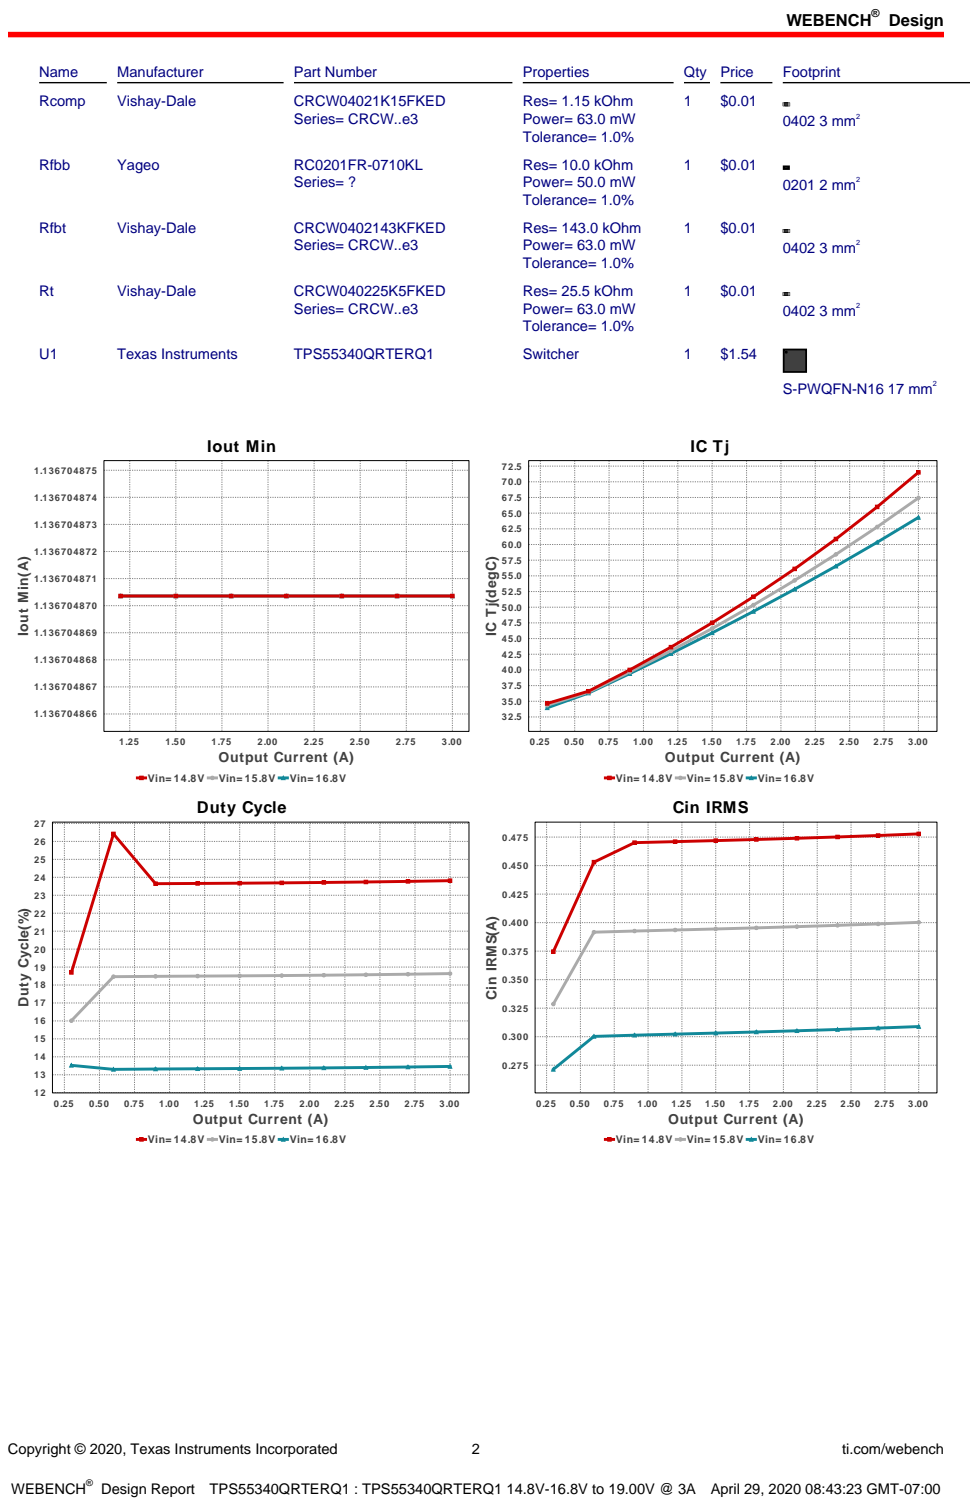
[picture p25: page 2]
Design; Copyright © 2020, Texas Instruments Incorporated; ti.com/webench; Name; Manufacturer; Part Number; Properties; Qty Price; Footprint; Rcomp; Vishay-Dale; CRCW04021K15FKED; Series= CRCW..e3; Res= 1.15 kOhm Power= 63.0 mW Tolerance= 1.0%; 0402 3 mm²; Rfbb; Yageo; Series= ?; Res= 10.0 kOhm Power= 50.0 mW Tolerance= 1.0%; 0201 2 mm²; Rfbt; CRCW0402143KFKED; Res= 143.0 kOhm Power= 63.0 mW Tolerance= 1.0%; CRCW040225K5FKED; Res= 25.5 kOhm Power= 63.0 mW Tolerance= 1.0%; Texas Instruments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

IC Tj(degC)

Vin= 14.8V Vin= 15.8V Vin= 16.8V
Duty Cycle

Cin IRMS

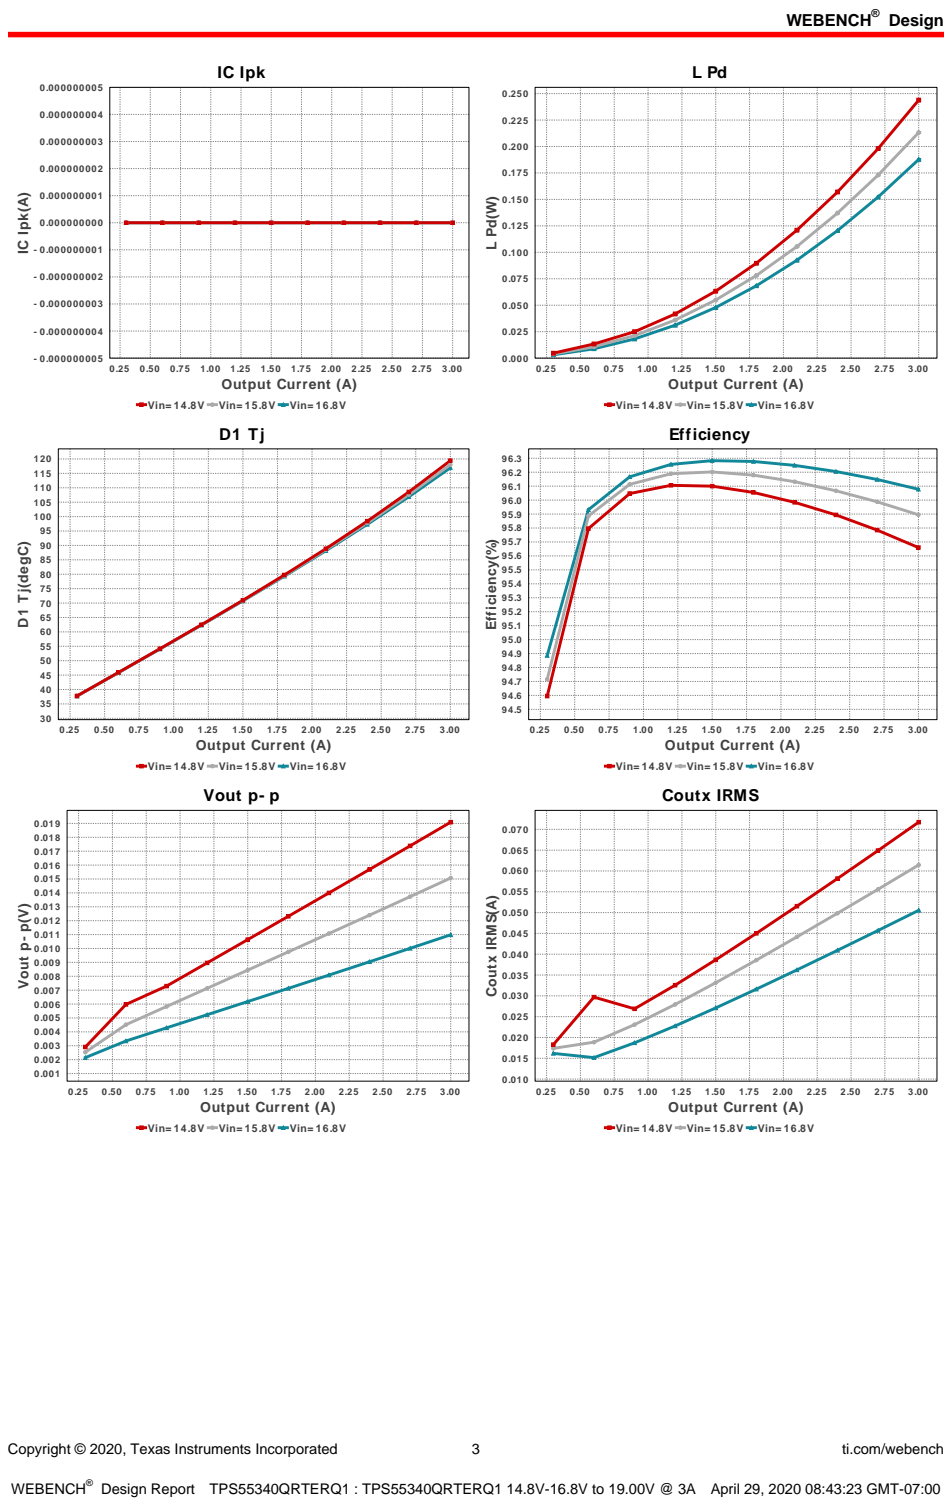
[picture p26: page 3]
Copyright © 2020, Texas Instruments Incorporated; ti.com/webench; IC Ipk; 0.25 0.50 0.75 1.00 1.25 1.50 1.75 2.00 2.25 2.50 2.75 3.00 Output Current (A); IC Ipk(A); 3.00 Output Current (A); D1 Tj(degC); Efficiency(%); Vout p- p(V); Coutx IRMS(A)

Vin= 14.8V Vin= 15.8V Vin= 16.8V

Efficiency

Vout p- p

Coutx IRMS

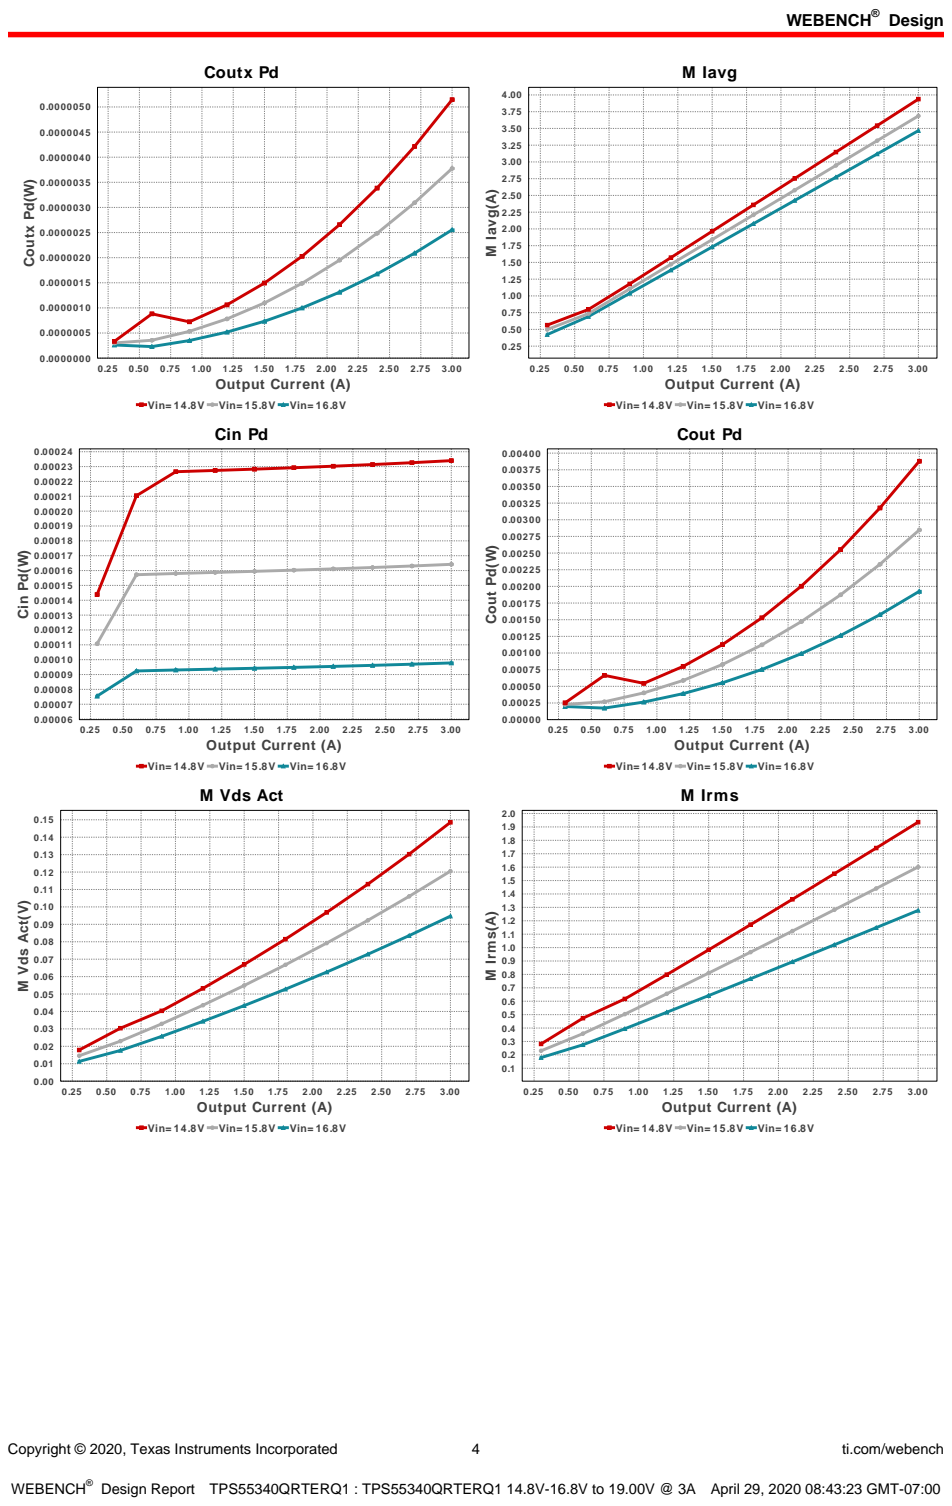
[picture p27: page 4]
Copyright © 2020, Texas Instruments Incorporated; ti.com/webench; Coutx Pd; 0.25 0.50 0.75 1.00 1.25 1.50 1.75 2.00 2.25 2.50 2.75 3.00 Output Current (A); Coutx Pd(W); M Iavg; 3.00 Output Current (A); M Iavg(A); Cin Pd; Cin Pd(W); Cout Pd; Cout Pd(W); M Vds Act(V); M Irms; M Irms(A)

Vin= 14.8V Vin= 15.8V Vin= 16.8V

M Vds Act
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

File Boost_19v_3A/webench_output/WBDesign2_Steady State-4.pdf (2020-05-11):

Cinx 100.0 nF 39.064 mOhm; Css 22.0 nF; 1.0 mOhm; Rfbb; 10.0 kOhm 50.0 mW; Ccomp 15.0 nF Ccomp2; Rt 25.5 kOhm; Cin 22.0 µF 2.05 mOhm Qty= 2; Cout 10.0 µF; 2.827 mOhm Qty= 2; D1 VF@Io= 560.0 mV VRRM= 60.0 V; L1 1.2 µH 15.5 mOhm; Rcomp 1.15 kOhm 63.0 mW; TPS55340- Q1; VIN; AGND; SYNC; COMP; FREQ; PGND; DNC; Rfbt 143.0 kOhm; Vout = 19.0V Iout = 3.0A; Coutx 1.0 µF 1.0 mOhm; Vin; Iout

Copyright © 2020, Texas Instruments Incorporated | 1 | ti.com/webench

WEBENCH®
Design Report TPS55340QRTERQ1 : TPS55340QRTERQ1 14.8V-16.8V to 19.00V @ 3A April 29, 2020 08:50:12 GMT-07:00

## WEBENCH ® Design Report

Design : 2 TPS55340QRTERQ1
TPS55340QRTERQ1 14.8V-16.8V to 19.00V @ 3A

VinMin = 14.8V
VinMax = 16.8V
Vout = 19.0V
Iout = 3.0A

Device = TPS55340QRTERQ1
Topology = Boost
Created = 2020-04-29 08:35:07.948 BOM Cost = $4.90
BOM Count = 16
Total Pd = 2.51W
1. For frequency > 1.6 MHz, the user is required to make sure load current is always greater than "Iout Min" value shown in the Op Vals.

### Design Alerts

Component Selection Information
The TPS55340-Q1 is qualified for Automotive applications. All passives and other components selected in this design may not be qualified for Automotive applications. The user is required to verify that all components in the design meet the qualification and safety requirements for their specific application.

## Electrical BOM

Name | Manufacturer | Part Number | Properties | Qty Price | Footprint
Ccomp | Kemet | C0603C153J3GACTU (http://www.kemet.com/docfinder?Partnumber%3DC0603C153J3GACTU) Series= C0G/NP0 | Cap= 15.0 nF VDC= 25.0 V IRMS= 0.0 A
1 | $0.10
| | | | | 0603 5 mm²
Ccomp2 | TDK | CGJ3E2C0G1H392J080AA (http://product.tdk.com/capacitor/mlcc/en/documents/mlcc%5Fhighreliability%5Fgeneral%5Fen.pdf) Series= C0G/NP0 | Cap= 3.9 nF VDC= 50.0 V IRMS= 0.0 A
1 | $0.07
| | | | | 0603 5 mm²
Cin | TDK | C2012X5R1V226M125AC Series= X5R | Cap= 22.0 uF ESR= 2.05 mOhm VDC= 35.0 V IRMS= 4.5559 A
2 | $0.33
| | | | | 0805 7 mm²
Cinx | TDK | CGA2B3X7R1H104K050BB (https://product.tdk.com/en/search/capacitor/ceramic/mlcc/info?part%5Fno%3DCGA2B3X7R1H104K050BB) Series= X7R

Cap= 100.0 nF
ESR= 39.064 mOhm
VDC= 50.0 V
IRMS= 814.67 mA

1 $0.02
0402 3 mm²
Cout | TDK | CGA6P3X7S1H106K250AB (https://product.tdk.com/en/search/capacitor/ceramic/mlcc/info?part%5Fno%3DCGA6P3X7S1H106K250AB) Series= X7S

Cap= 10.0 uF
ESR= 2.827 mOhm
VDC= 50.0 V
IRMS= 4.3729 A

2 $0.33
1210_280 15 mm²
Coutx | Taiyo Yuden | GMK212B7105KG-T (http://www.yuden.co.jp/ut/product/pdf/djmk%5Fe.pdf) Series= X7R

Cap= 1.0 uF
ESR= 1.0 mOhm
VDC= 35.0 V
IRMS= 0.0 A

1 $0.03
0805 7 mm²
Css | MuRata | GRM155R71C223KA01D (http://search.murata.co.jp/Ceramy/PnsearchViewAction.do) Series= X7R

Cap= 22.0 nF
ESR= 1.0 mOhm
VDC= 16.0 V
IRMS= 0.0 A

1 $0.01
0402 3 mm²
D1 | Diodes Inc. | PDS760-13 | VF@Io= 560.0 mV VRRM= 60.0 V
1 | $0.63

PowerDI5 50 mm²
L1 | Wurth Elektronik | 74438357012 (http://katalog.we%2Donline.de/pbs/datasheet/74438357012.pdf) | L= 1.2 µH 15.5 mOhm
1 | $1.14
WE-MAPI_4030 26 mm²

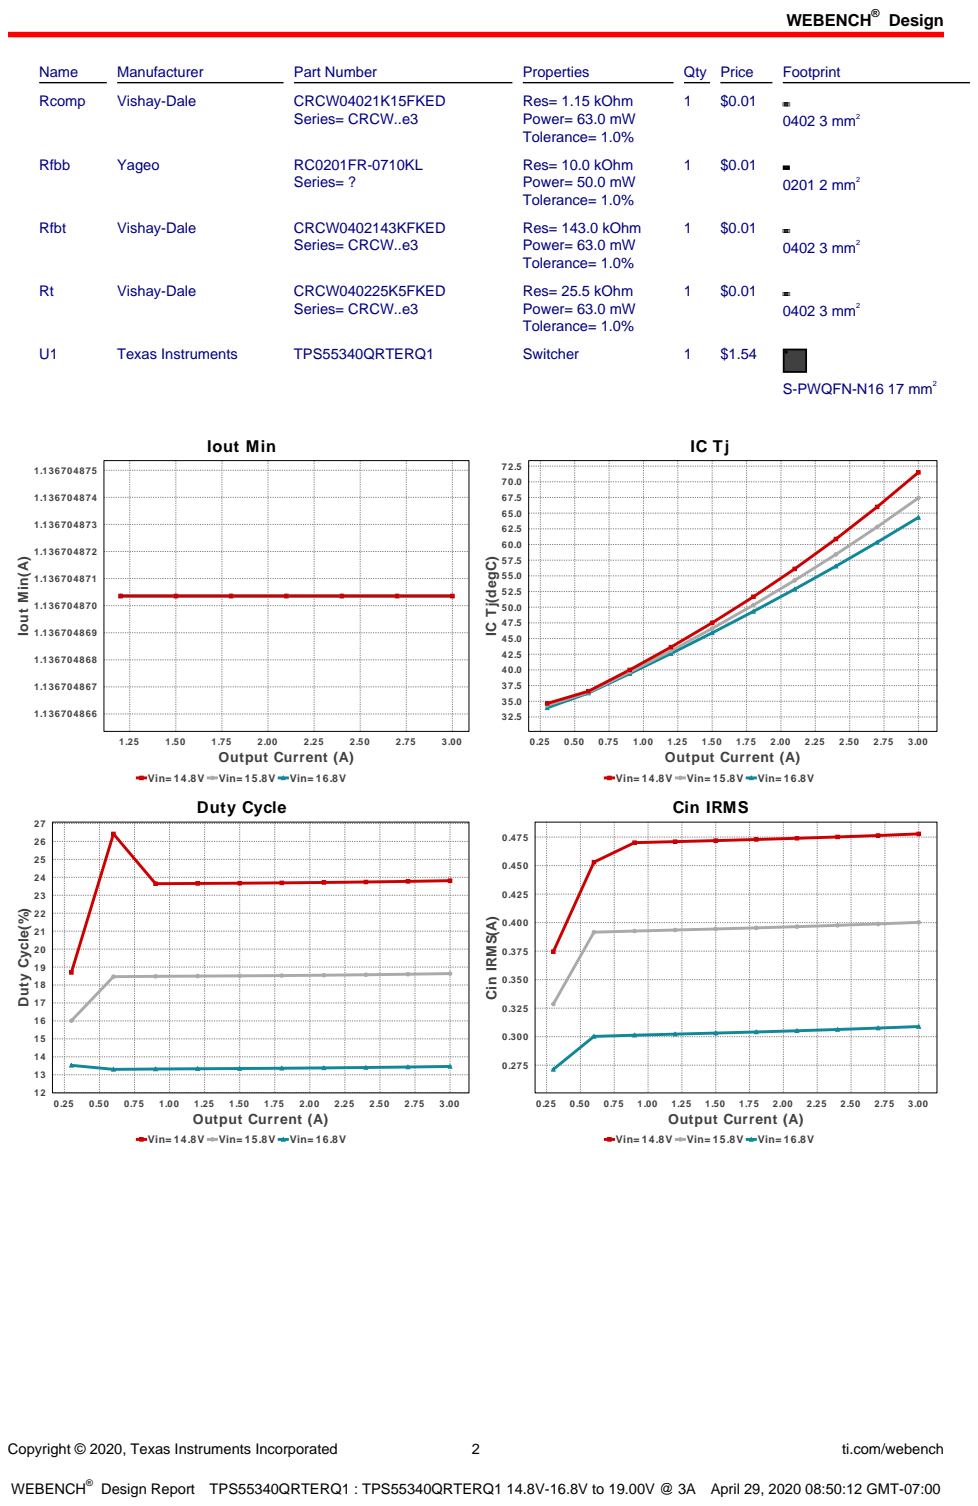
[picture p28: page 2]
Design; Copyright © 2020, Texas Instruments Incorporated; ti.com/webench; Name; Manufacturer; Part Number; Properties; Qty Price; Footprint; Rcomp; Vishay-Dale; CRCW04021K15FKED; Series= CRCW..e3; Res= 1.15 kOhm Power= 63.0 mW Tolerance= 1.0%; 0402 3 mm²; Rfbb; Yageo; Series= ?; Res= 10.0 kOhm Power= 50.0 mW Tolerance= 1.0%; 0201 2 mm²; Rfbt; CRCW0402143KFKED; Res= 143.0 kOhm Power= 63.0 mW Tolerance= 1.0%; CRCW040225K5FKED; Res= 25.5 kOhm Power= 63.0 mW Tolerance= 1.0%; Texas Instruments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

IC Tj(degC)

Vin= 14.8V Vin= 15.8V Vin= 16.8V
Duty Cycle

Cin IRMS

Copyright © 2020, Texas Instruments Incorporated; ti.com/webench; IC Ipk; 0.25 0.50 0.75 1.00 1.25 1.50 1.75 2.00 2.25 2.50 2.75 3.00 Output Current (A); IC Ipk(A); 3.00 Output Current (A); D1 Tj(degC); Efficiency(%); Vout p- p(V); Coutx IRMS(A)

Vin= 14.8V Vin= 15.8V Vin= 16.8V

Efficiency

Vout p- p

Coutx IRMS

Copyright © 2020, Texas Instruments Incorporated; ti.com/webench; Coutx Pd; 0.25 0.50 0.75 1.00 1.25 1.50 1.75 2.00 2.25 2.50 2.75 3.00 Output Current (A); Coutx Pd(W); M Iavg; 3.00 Output Current (A); M Iavg(A); Cin Pd; Cin Pd(W); Cout Pd; Cout Pd(W); M Vds Act(V); M Irms; M Irms(A)

Vin= 14.8V Vin= 15.8V Vin= 16.8V

M Vds Act
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

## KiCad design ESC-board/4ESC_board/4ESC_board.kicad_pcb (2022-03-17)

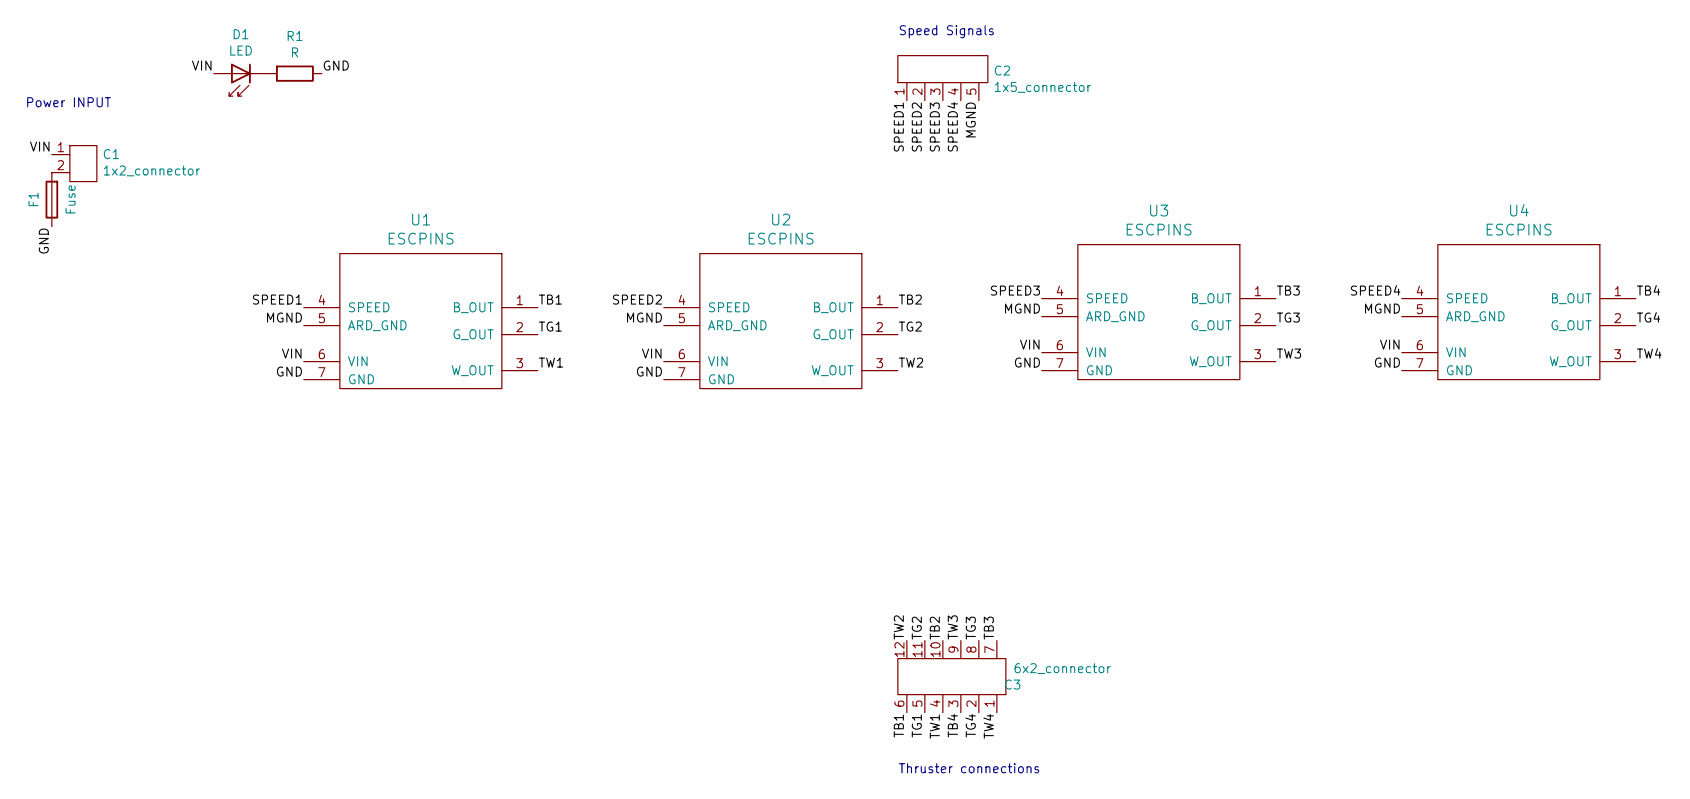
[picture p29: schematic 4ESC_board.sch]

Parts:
C1: 1x2_connector; molex_supersabre_1x2_172043-0201
C2: 1x5_connector; Molex_Microfit_1x5_436500500
C3: 6x2_connector; Molex_microfit_2x6_444281201
D1: LED; D_1206_3216Metric_Pad1.42x1.75mm_HandSolder
F1: Fuse; MCCQ-122
R1: R; R_1206_3216Metric_Pad1.42x1.75mm_HandSolder
U1, U2, U3, U4: ESCPINS; ESC_footprint

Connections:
/GND: F1.1, R1.1, U1.7 (GND), U2.7 (GND), U3.7 (GND), U4.7 (GND)
/MGND: C2.5, U1.5 (ARD_GND), U2.5 (ARD_GND), U3.5 (ARD_GND), U4.5 (ARD_GND)
/SPEED1: C2.1, U1.4 (SPEED)
/SPEED2: C2.2, U2.4 (SPEED)
/SPEED3: C2.3, U3.4 (SPEED)
/SPEED4: C2.4, U4.4 (SPEED)
/TB1: C3.6, U1.1 (B_OUT)
/TB2: C3.10, U2.1 (B_OUT)
/TB3: C3.7, U3.1 (B_OUT)
/TB4: C3.3, U4.1 (B_OUT)
/TG1: C3.5, U1.2 (G_OUT)
/TG2: C3.11, U2.2 (G_OUT)
/TG3: C3.8, U3.2 (G_OUT)
/TG4: C3.2, U4.2 (G_OUT)
/TW1: C3.4, U1.3 (W_OUT)
/TW2: C3.12, U2.3 (W_OUT)
/TW3: C3.9, U3.3 (W_OUT)
/TW4: C3.1, U4.3 (W_OUT)
/VIN: C1.1, D1.2 (A), U1.6 (VIN), U2.6 (VIN), U3.6 (VIN), U4.6 (VIN)
unnamed: C1.2, F1.2
unnamed: D1.1 (K), R1.2

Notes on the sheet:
Power INPUT
Speed Signals
Thruster connections

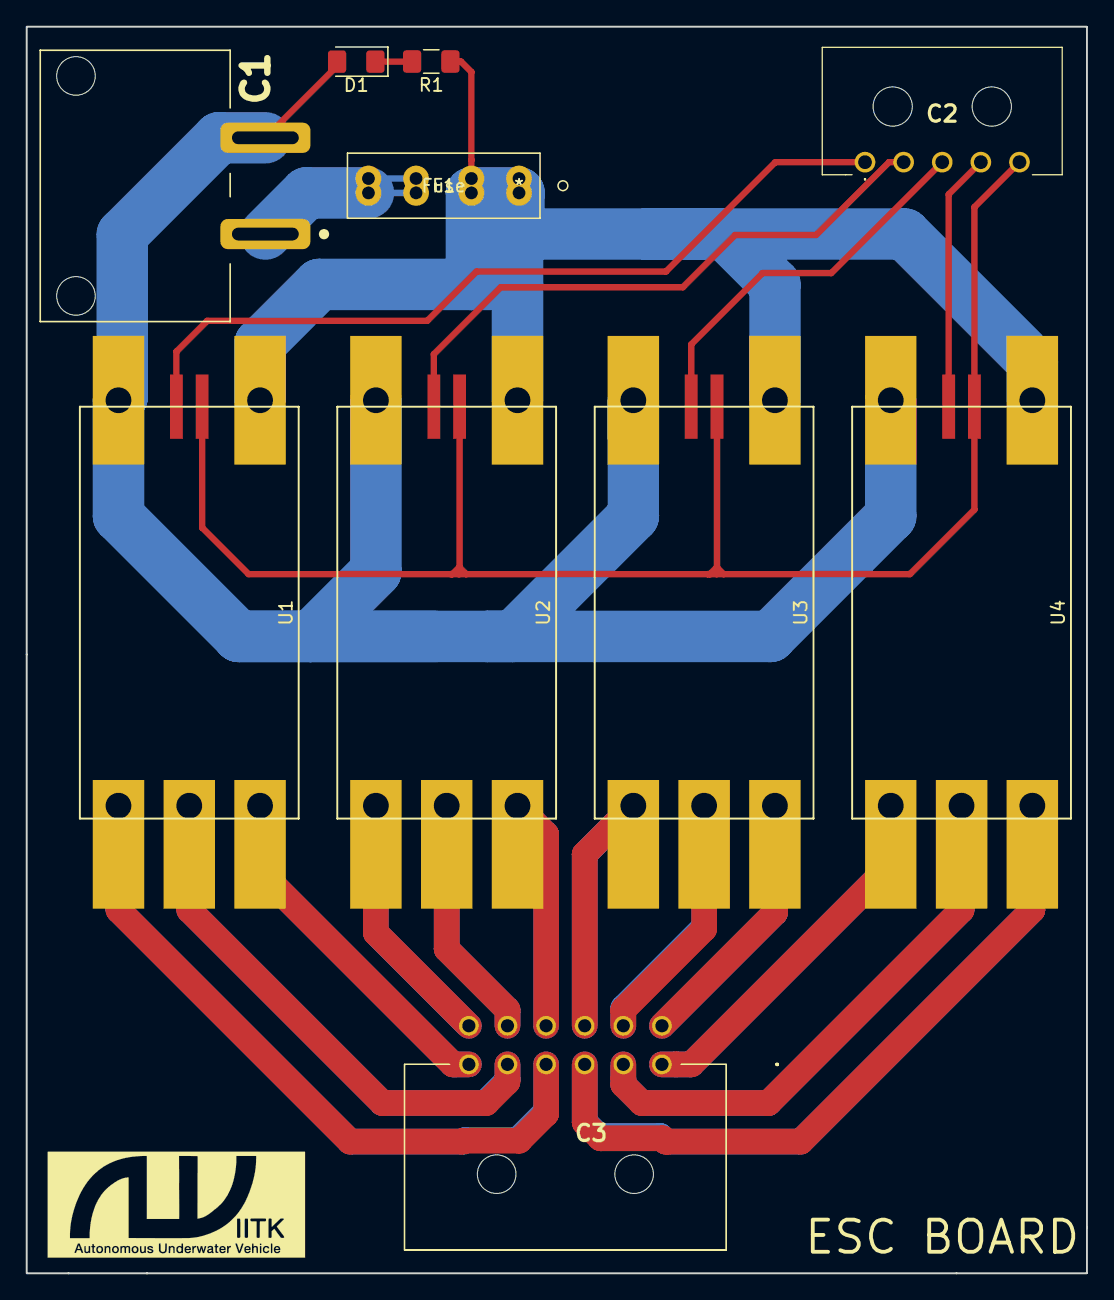
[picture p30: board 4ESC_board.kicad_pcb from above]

Board: 2 copper layers, 82.4 x 96.9 mm, 10 parts (0 on the bottom side), 21 nets.

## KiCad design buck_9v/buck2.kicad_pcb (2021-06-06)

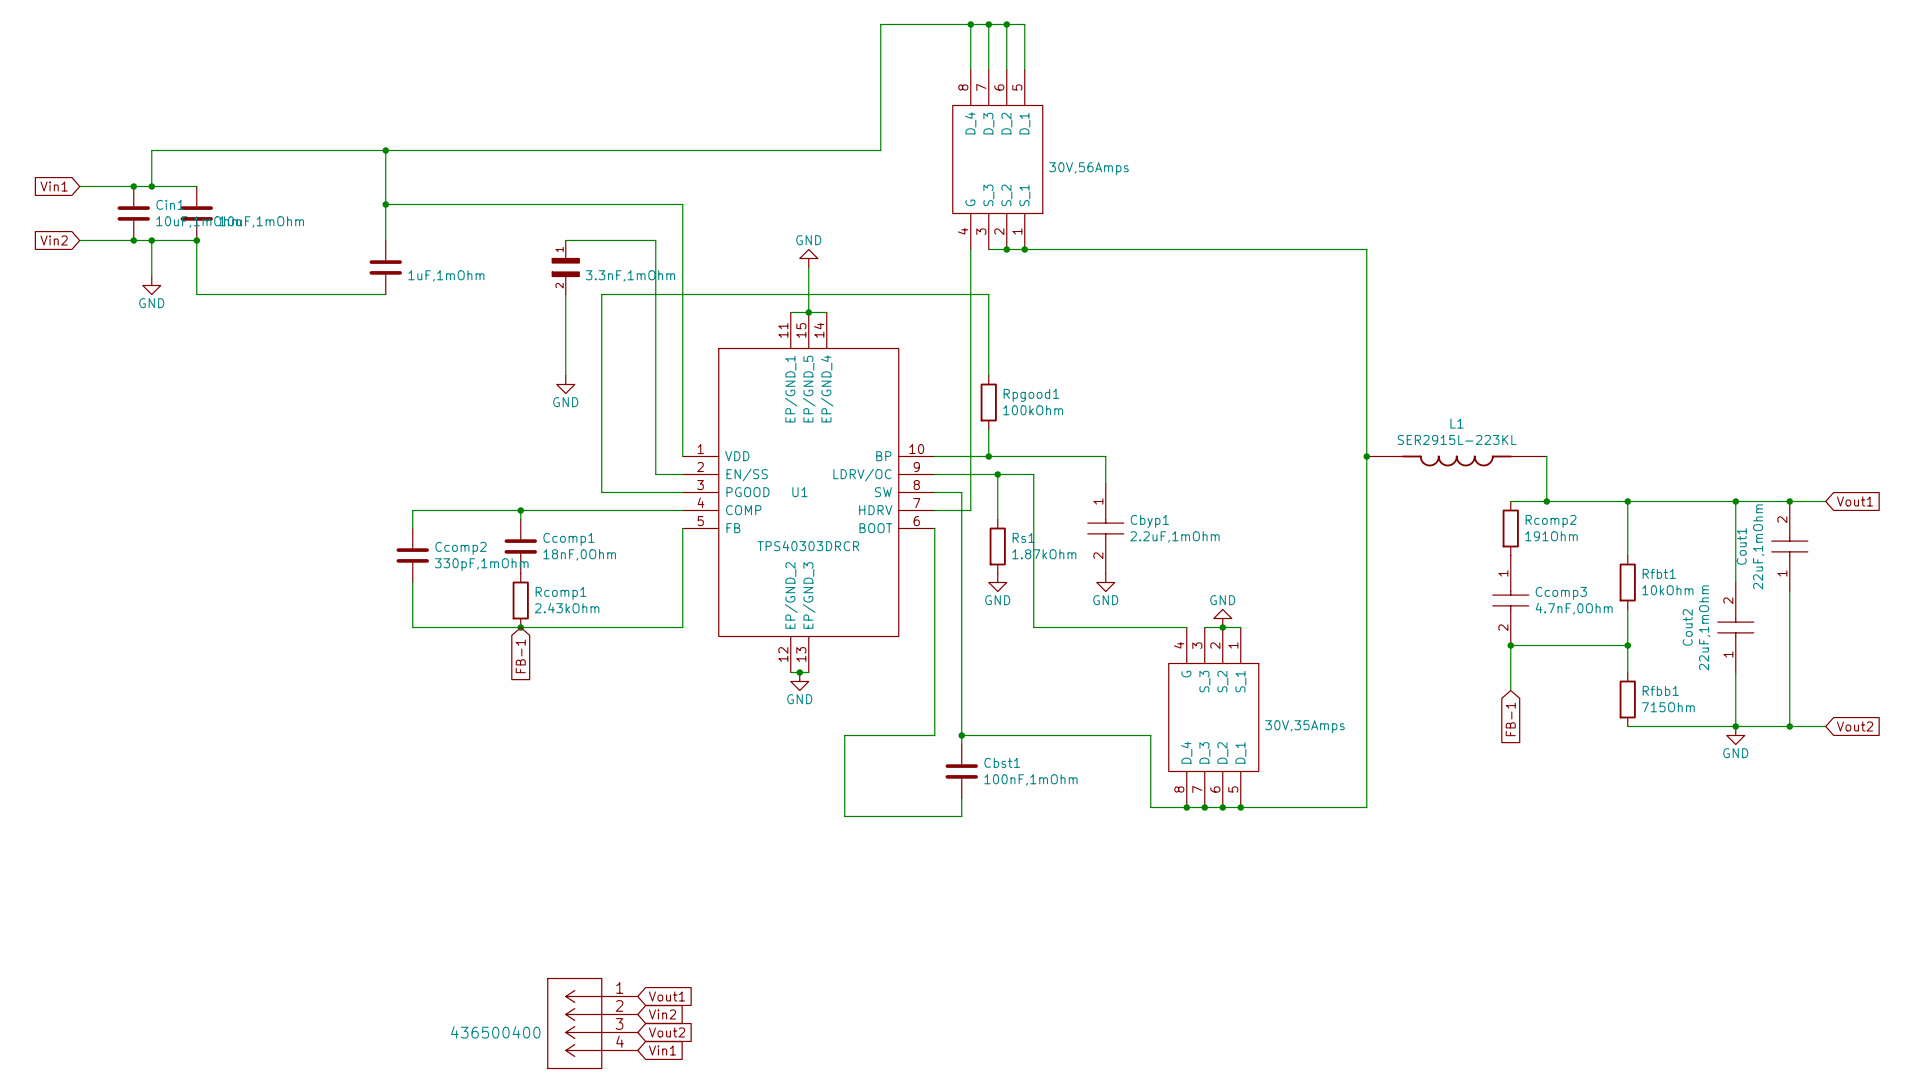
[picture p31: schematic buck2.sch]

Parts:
Cbst1: 100nF,1mOhm; C_0402_1005Metric
Cbyp1: 2.2uF,1mOhm; CAPC2012X135N; Mouser Part Number 963-EMK212BJ225KG-T
Ccomp1: 18nF,0Ohm; C_1812_4532Metric
Ccomp2: 330pF,1mOhm; C_0402_1005Metric
Ccomp3: 4.7nF,0Ohm; CAPC2012X75N; Mouser Part Number 810-CGA4C2C0G1H472J
Cin1, Cin2: 10uF,1mOhm; C_1210_3225Metric
Cout1, Cout2: 22uF,1mOhm; CAPC3225X270N; Mouser Part Number 963-TMK325B7226KMHP
Css1: 3.3nF,1mOhm; CAPC0603X33N
Cvcc1: 1uF,1mOhm; C_0805_2012Metric
J1: 436500400
L1: SER2915L-223KL; IND_SER2915L-223KL
M1: 30V,56Amps; DQG_VSON-CLIP; Mouser Part Number 595-CSD17304Q3
M2: 30V,35Amps; Q3A; Mouser Part Number 595-CSD17577Q3A
Rcomp1: 2.43kOhm; R_0402_1005Metric
Rcomp2: 191Ohm; R_0402_1005Metric
Rfbb1: 715Ohm; R_0402_1005Metric
Rfbt1: 10kOhm; R_0201_0603Metric
Rpgood1: 100kOhm; R_0402_1005Metric
Rs1: 1.87kOhm; R_0402_1005Metric
U1: TPS40303DRCR; Manufacturer_Part_Number TPS40303DRCR

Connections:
FB-1: Ccomp2.2, Ccomp3.2, Rcomp1.2, Rfbb1.1, Rfbt1.2, U1.5 (FB)
unnamed: Cbst1.1, U1.6 (BOOT)
unnamed: Cbst1.2, L1.1, M1.1 (S_1), M1.2 (S_2), M1.3 (S_3), M2.5 (D_1), M2.6 (D_2), M2.7 (D_3), M2.8 (D_4), U1.8 (SW)
unnamed: Cbyp1.1, Rpgood1.2, U1.10 (BP)
unnamed: Ccomp1.1, Rcomp1.1
unnamed: Ccomp1.2, Ccomp2.1, U1.4 (COMP)
unnamed: Ccomp3.1, Rcomp2.2
unnamed: Css1.1, U1.2 (EN/SS)
unnamed: M1.4 (G), U1.7 (HDRV)
unnamed: M2.4 (G), Rs1.1, U1.9 (LDRV/OC)
unnamed: Rpgood1.1, U1.3 (PGOOD)
Vin1: Cin1.1, Cin2.1, Cvcc1.2, J1.4, M1.5 (D_1), M1.6 (D_2), M1.7 (D_3), M1.8 (D_4), U1.1 (VDD)
Vin2: Cbyp1.2, Cin1.2, Cin2.2, Cout1.1, Cout2.1, Css1.2, Cvcc1.1, J1.2, J1.3, M2.1 (S_1), M2.2 (S_2), M2.3 (S_3), Rfbb1.2, Rs1.2, U1.11 (EP/GND_1), U1.12 (EP/GND_2), U1.13 (EP/GND_3), U1.14 (EP/GND_4), U1.15 (EP/GND_5)
Vout1: Cout1.2, Cout2.2, J1.1, L1.2, Rcomp2.1, Rfbt1.1

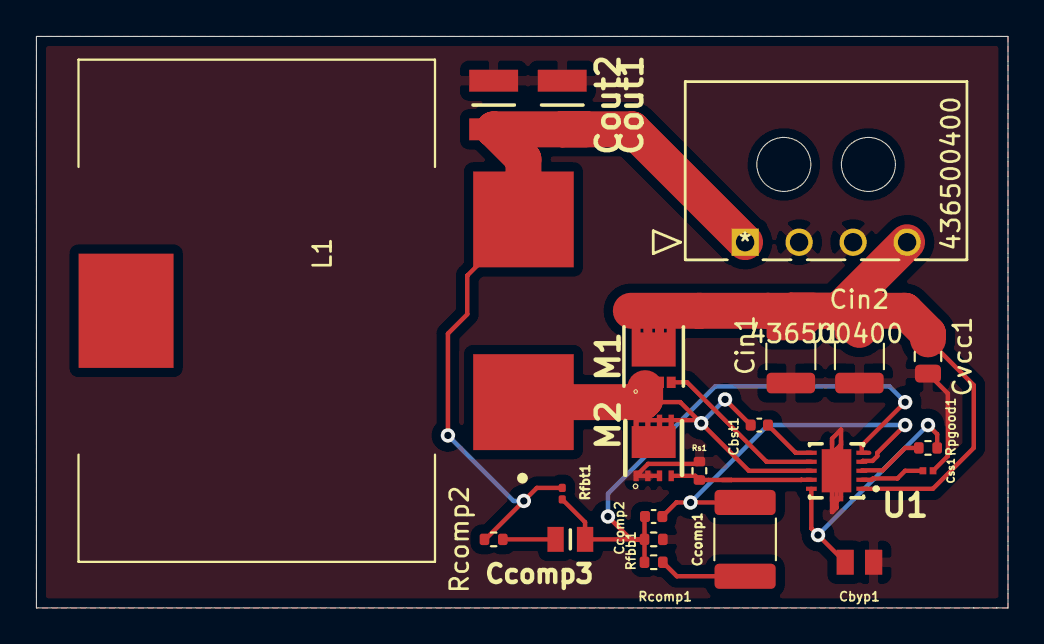
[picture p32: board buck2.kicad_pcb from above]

Board: 2 copper layers, 54.0 x 31.8 mm, 22 parts (0 on the bottom side), 14 nets.

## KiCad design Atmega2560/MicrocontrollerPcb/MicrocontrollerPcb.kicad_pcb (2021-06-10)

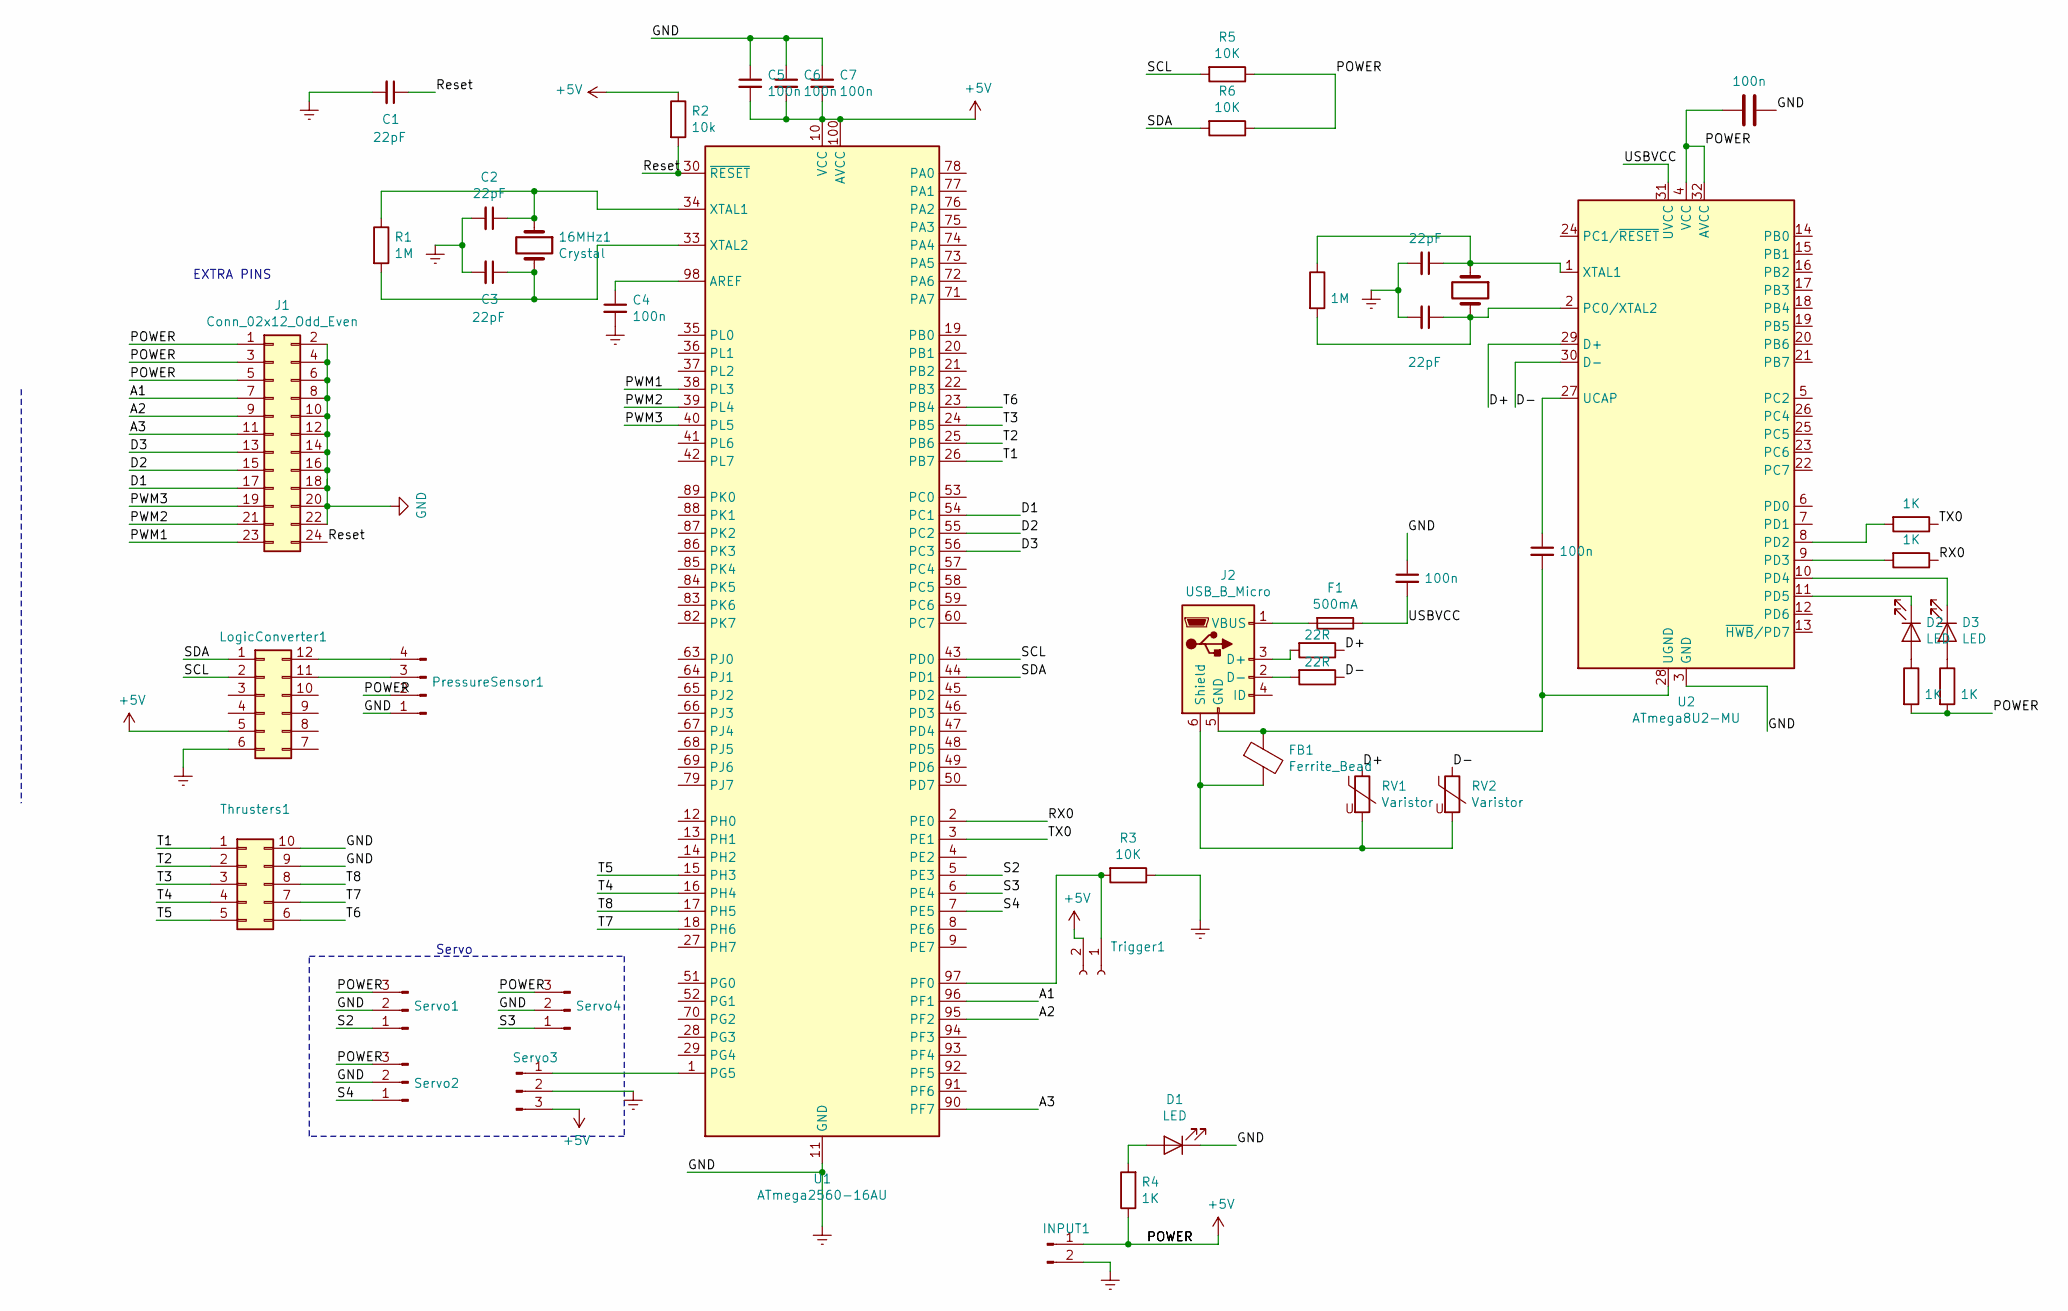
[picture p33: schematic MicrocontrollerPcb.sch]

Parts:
16MHz1, 16MHz2: Crystal; Crystal_HC49-U_Vertical
C1, C2, C3, C9, C10: 22pF; C_0805_2012Metric_Pad1.15x1.40mm_HandSolder
C4, C5, C6, C7, C8, C11, C12: 100n; C_0603_1608Metric_Pad1.05x0.95mm_HandSolder
D1, D2, D3: LED; LED_1206_3216Metric
F1: 500mA; Fuse_1206_3216Metric_Pad1.42x1.75mm_HandSolder
FB1: Ferrite_Bead; R_0805_2012Metric
INPUT1: Conn_01x02_Male; input
J1: Conn_02x12_Odd_Even; PinHeader_2x12_P2.54mm_Vertical
J2: USB_B_Micro; USB_Micro-B_Amphenol_10103594-0001LF_Horizontal
LogicConverter1: Conn_02x06_Counter_Clockwise; 02x06
PressureSensor1: Conn_01x04_Male; 53375-0410
R1, R7: 1M; R_0402_1005Metric
R2: 10k; R_0402_1005Metric
R3, R5, R6: 10K; R_0402_1005Metric
R4, R10, R11, R12, R13: 1K; R_1206_3216Metric_Pad1.42x1.75mm_HandSolder
R8, R9: 22R; R_0603_1608Metric_Pad1.05x0.95mm_HandSolder
RV1, RV2: Varistor; R_0603_1608Metric_Pad1.05x0.95mm_HandSolder
Servo1, Servo2, Servo3, Servo4: Conn_01x03_Male; 01x03
Thrusters1: Connector 02x05; 02x05
Trigger1: Conn_01x02_Female; 53375-0210
U1: ATmega2560-16AU; TQFP-100_14x14mm_P0.5mm
U2: ATmega8U2-MU; QFN-32-1EP_5x5mm_P0.5mm_EP3.1x3.1mm

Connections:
+5V: C5.2, C6.2, C7.2, C12.2, INPUT1.1, J1.1, J1.3, J1.5, LogicConverter1.5, PressureSensor1.2, R2.1, R4.1, R5.1, R6.1, R12.2, R13.2, Servo1.3, Servo2.3, Servo3.3, Servo4.3, Trigger1.2, U1.10 (VCC), U1.31 (VCC), U1.61 (VCC), U1.80 (VCC), U1.100 (AVCC), U2.4 (VCC), U2.32 (AVCC)
/A1: J1.7, U1.96 (PF1)
/A2: J1.9, U1.95 (PF2)
/A3: J1.11, U1.90 (PF7)
/D1: J1.17, U1.54 (PC1)
/D2: J1.15, U1.55 (PC2)
/D3: J1.13, U1.56 (PC3)
/D+: R8.1, RV1.1, U2.29 (D+)
/D-: R9.1, RV2.1, U2.30 (D-)
/PWM1: J1.23, U1.38 (PL3)
/PWM2: J1.21, U1.39 (PL4)
/PWM3: J1.19, U1.40 (PL5)
/RX0: R11.1, U1.2 (PE0)
/Reset: C1.1, J1.24, R2.2, U1.30 (~RESET)
/S2: Servo1.1, U1.5 (PE3)
/S3: Servo4.1, U1.6 (PE4)
/S4: Servo2.1, U1.7 (PE5)
/SCL: LogicConverter1.2, R5.2, U1.43 (PD0)
/SDA: LogicConverter1.1, R6.2, U1.44 (PD1)
/T1: Thrusters1.1, U1.26 (PB7)
/T2: Thrusters1.2, U1.25 (PB6)
/T3: Thrusters1.3, U1.24 (PB5)
/T4: Thrusters1.4, U1.16 (PH4)
/T5: Thrusters1.5, U1.15 (PH3)
/T6: Thrusters1.6, U1.23 (PB4)
/T7: Thrusters1.7, U1.18 (PH6)
/T8: Thrusters1.8, U1.17 (PH5)
/TX0: R10.1, U1.3 (PE1)
/USBVCC: C8.2, F1.1, U2.31 (UVCC)
Earth: C1.2, C2.2, C3.2, C4.2, C5.1, C6.1, C7.1, C8.1, C9.2, C10.2, C12.1, D1.1 (K), INPUT1.2, J1.2, J1.4, J1.6, J1.8, J1.10, J1.12, J1.14, J1.16, J1.18, J1.20, J1.22, LogicConverter1.6, PressureSensor1.1, R3.1, Servo1.2, Servo2.2, Servo3.2, Servo4.2, Thrusters1.9, Thrusters1.10, U1.11 (GND), U1.32 (GND), U1.62 (GND), U1.81 (GND), U1.99 (GND), U2.3 (GND), U2.33 (GND)
unnamed: 16MHz1.1, C2.1, R1.1, U1.34 (XTAL1)
unnamed: 16MHz1.2, C3.1, R1.2, U1.33 (XTAL2)
unnamed: 16MHz2.1, C9.1, R7.1, U2.1 (XTAL1)
unnamed: 16MHz2.2, C10.1, R7.2, U2.2 (PC0/XTAL2)
unnamed: C4.1, U1.98 (AREF)
unnamed: C11.1, U2.27 (UCAP)
unnamed: C11.2, FB1.1, J2.5 (GND), U2.28 (UGND)
unnamed: D1.2 (A), R4.2
unnamed: D2.1 (K), U2.11 (PD5)
unnamed: D2.2 (A), R12.1
unnamed: D3.1 (K), U2.10 (PD4)
unnamed: D3.2 (A), R13.1
unnamed: F1.2, J2.1 (VBUS)
unnamed: FB1.2, J2.6 (Shield), RV1.2, RV2.2
unnamed: J2.2 (D-), R9.2
unnamed: J2.3 (D+), R8.2
unnamed: LogicConverter1.11, PressureSensor1.3
unnamed: LogicConverter1.12, PressureSensor1.4
unnamed: R3.2, Trigger1.1, U1.97 (PF0)
unnamed: R10.2, U2.8 (PD2)
unnamed: R11.2, U2.9 (PD3)
unnamed: Servo3.1, U1.1 (PG5)

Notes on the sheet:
EXTRA PINS
Servo

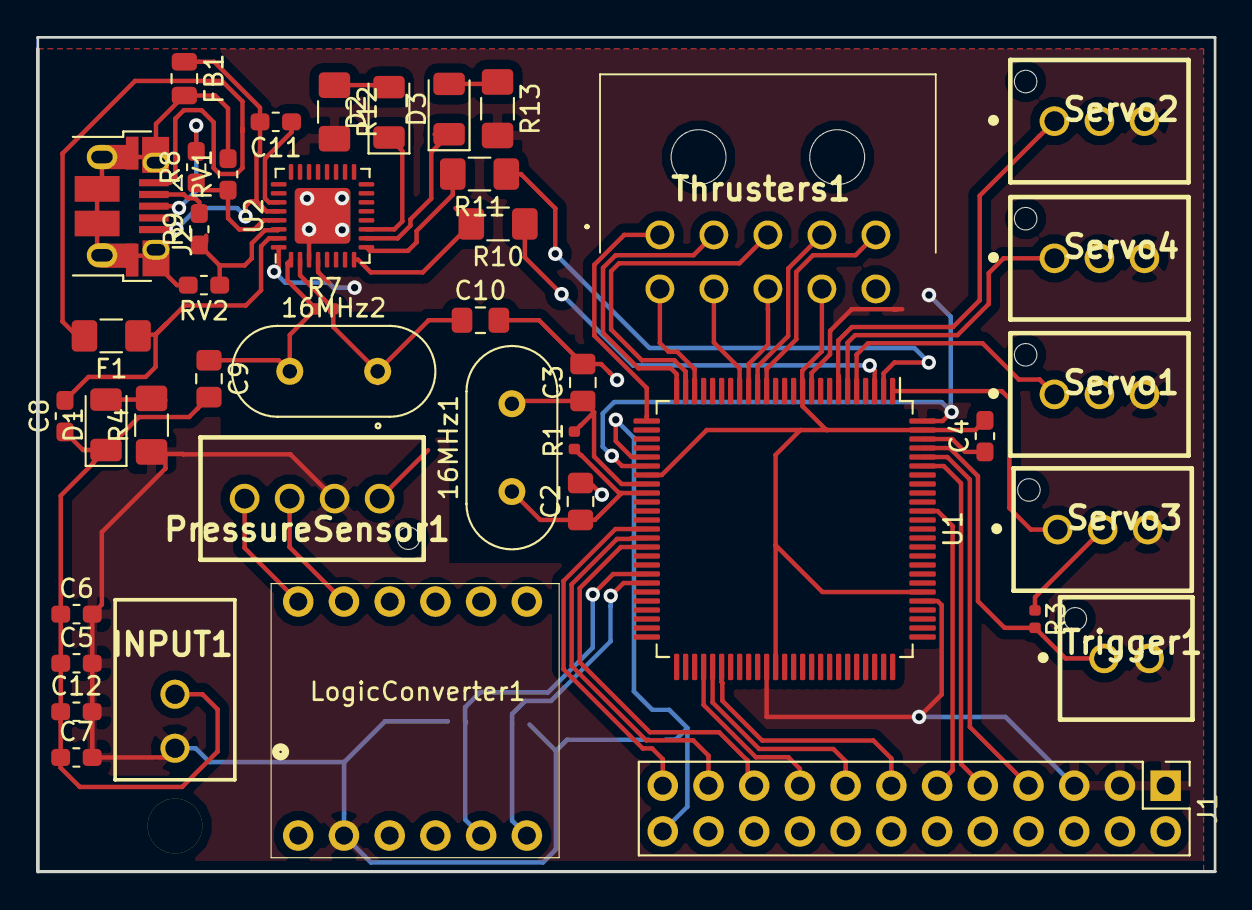
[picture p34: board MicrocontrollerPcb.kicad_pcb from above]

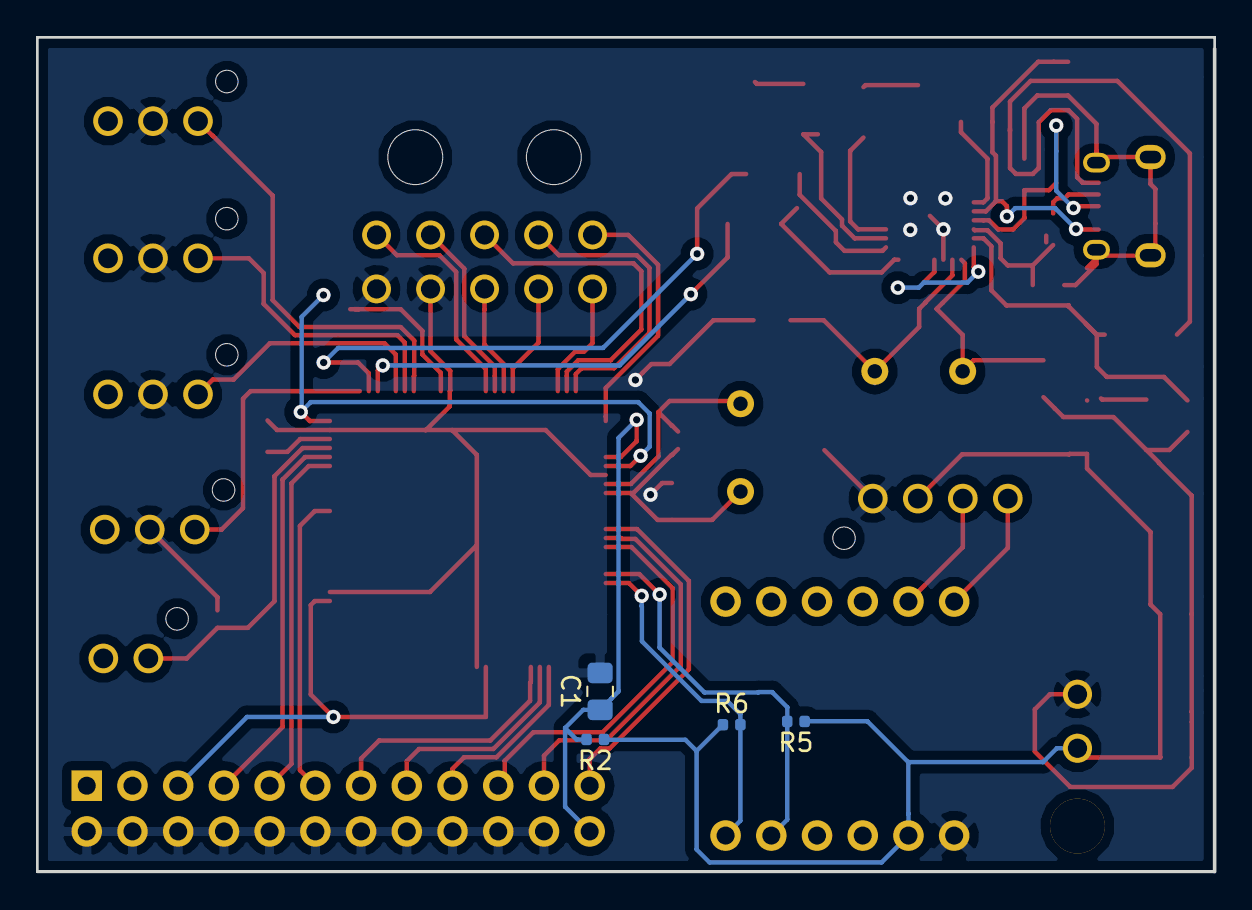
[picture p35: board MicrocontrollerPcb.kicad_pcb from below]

Board: 2 copper layers, 65.4 x 46.4 mm, 47 parts (4 on the bottom side), 52 nets.

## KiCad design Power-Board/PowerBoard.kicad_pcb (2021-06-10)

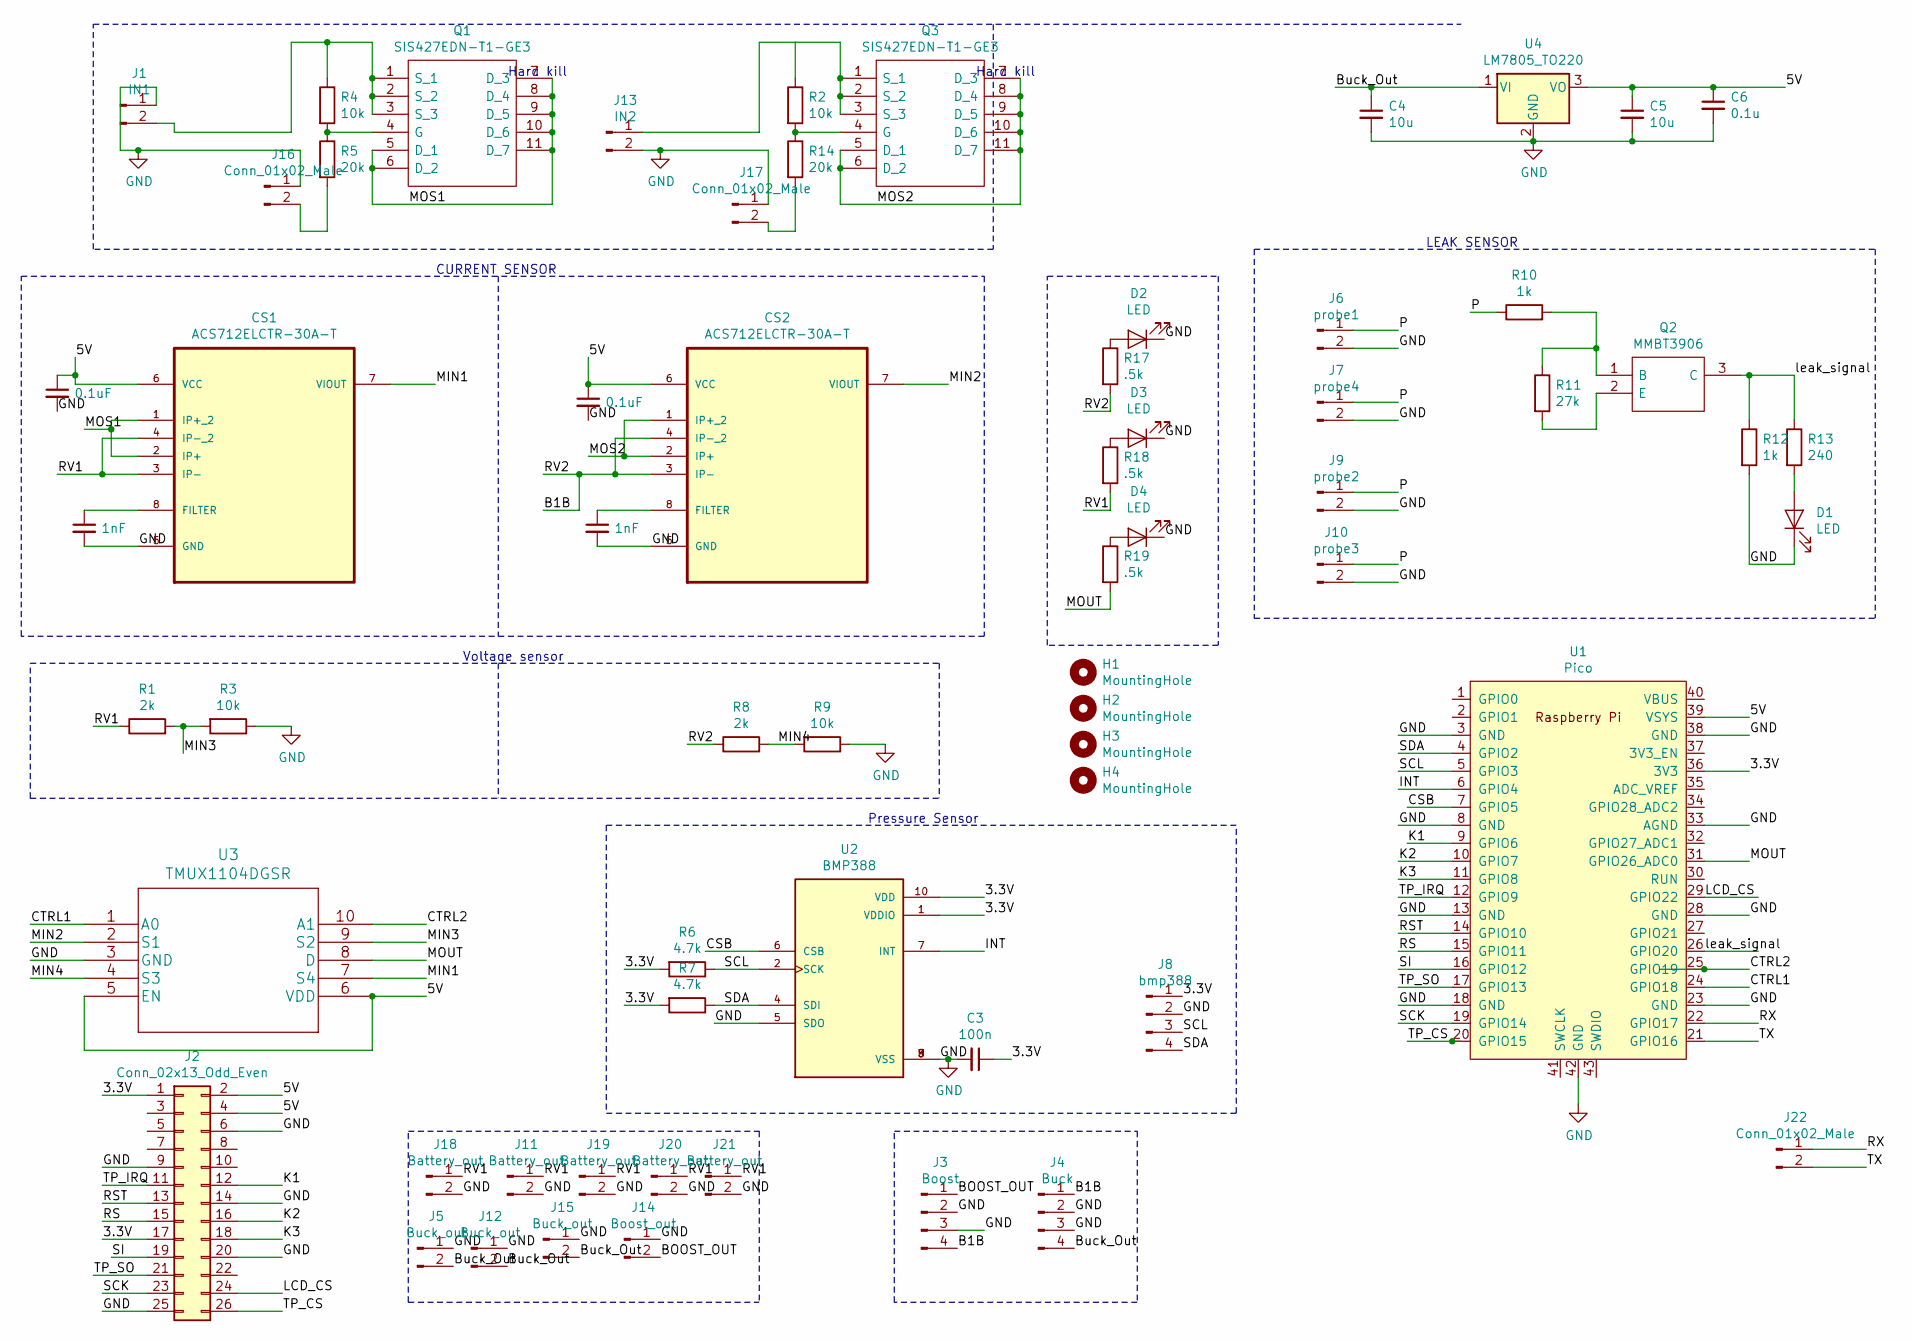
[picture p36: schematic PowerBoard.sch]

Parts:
C1, C8: 1nF; C_0603_1608Metric_Pad1.05x0.95mm_HandSolder
C2, C7: 0.1uF; C_0603_1608Metric_Pad1.05x0.95mm_HandSolder
C3: 100n; C_0603_1608Metric_Pad1.05x0.95mm_HandSolder
C4, C5: 10u; C_0603_1608Metric_Pad1.05x0.95mm_HandSolder
C6: 0.1u; C_0603_1608Metric_Pad1.05x0.95mm_HandSolder
CS1, CS2: ACS712ELCTR-30A-T; SOIC127P600X175-8N
D1, D2, D3, D4: LED; LED_0603_1608Metric
H1, H2, H3, H4: MountingHole; MountingHole_3.2mm_M3
J1: IN1; molex_supersabre_1x2_172043-0201
J2: Conn_02x13_Odd_Even; PinHeader_2x13_P2.54mm_Vertical
J3: Boost; CON_436500400_MOL
J4: Buck; CON_436500400_MOL
J5, J12, J15: Buck_out; input
J6: probe1; 01x02
J7: probe4; 01x02
J8: bmp388; PinHeader_1x04_P2.54mm_Vertical
J9: probe2; 01x02
J10: probe3; 01x02
J11: Battery_out; molex_supersabre_1x2_172043-0201
J13: IN2; molex_supersabre_1x2_172043-0201
J14: Boost_out; input
J16, J17, J22: Conn_01x02_Male; 01x02
J18, J19, J20, J21: Battery_out; input
Q1, Q3: SIS427EDN-T1-GE3; SIS862DNT1GE3; Mouser Part Number 78-SIS427EDN-T1-GE3
Q2: MMBT3906; SOT95P240X120-3N; Mouser Part Number 512-MMBT3906
R1, R8: 2k; R_0603_1608Metric_Pad1.05x0.95mm_HandSolder
R2, R3, R4, R9: 10k; R_0603_1608Metric_Pad1.05x0.95mm_HandSolder
R5, R14: 20k; R_0603_1608Metric_Pad1.05x0.95mm_HandSolder
R6, R7: 4.7k; R_0603_1608Metric_Pad1.05x0.95mm_HandSolder
R10, R12: 1k; R_0603_1608Metric_Pad1.05x0.95mm_HandSolder
R11: 27k; R_0603_1608Metric_Pad1.05x0.95mm_HandSolder
R13: 240; R_0805_2012Metric_Pad1.15x1.40mm_HandSolder
R17, R18, R19: .5k; R_0603_1608Metric_Pad1.05x0.95mm_HandSolder
U1: Pico; RPi_Pico_SMD_TH
U2: BMP388; PQFN50P200X200X80-10N; PARTREV 1.1
U3: TMUX1104DGSR; DGS10_TEX
U4: LM7805_TO220; TO-220-3_Vertical

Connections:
/3.3V: C3.1, J2.1, J2.17, J8.1, R6.2, R7.2, U1.36 (3V3), U2.1 (VDDIO), U2.10 (VDD)
/5V: C2.1, C5.1, C6.1, C7.1, CS1.6 (VCC), CS2.6 (VCC), J2.2, J2.4, U1.39 (VSYS), U3.5 (EN), U3.6 (VDD), U4.3 (VO)
/B1B: CS2.3 (IP-), CS2.4 (IP-_2), J3.4, J4.1, R8.1, R17.2
/BOOST_OUT: J3.1, J14.2
/Buck_Out: C4.1, J4.4, J5.2, J12.2, J15.2, U4.1 (VI)
/CSB: U1.7 (GPIO5), U2.6 (CSB)
/CTRL1: U1.24 (GPIO18), U3.1 (A0)
/CTRL2: U1.25 (GPIO19), U3.10 (A1)
/INT: U1.6 (GPIO4), U2.7 (INT)
/K1: J2.12, U1.9 (GPIO6)
/K2: J2.16, U1.10 (GPIO7)
/K3: J2.18, U1.11 (GPIO8)
/LCD_CS: J2.24, U1.29 (GPIO22)
/MIN1: CS1.7 (VIOUT), U3.7 (S4)
/MIN2: CS2.7 (VIOUT), U3.2 (S1)
/MIN3: R1.2, R3.2, U3.9 (S2)
/MIN4: R8.2, R9.2, U3.4 (S3)
/MOS1: CS1.1 (IP+_2), CS1.2 (IP+), Q1.5 (D_1), Q1.6 (D_2), Q1.7 (D_3), Q1.8 (D_4), Q1.9 (D_5), Q1.10 (D_6), Q1.11 (D_7)
/MOS2: CS2.1 (IP+_2), CS2.2 (IP+), Q3.5 (D_1), Q3.6 (D_2), Q3.7 (D_3), Q3.8 (D_4), Q3.9 (D_5), Q3.10 (D_6), Q3.11 (D_7)
/MOUT: R19.2, U1.31 (GPIO26_ADC0), U3.8 (D)
/P: J6.1, J7.1, J9.1, J10.1, R10.1
/RS: J2.15, U1.15 (GPIO11)
/RST: J2.13, U1.14 (GPIO10)
/RV1: CS1.3 (IP-), CS1.4 (IP-_2), J11.1, J18.1, J19.1, J20.1, J21.1, R1.1, R18.2
/RX: J22.1, U1.22 (GPIO17)
/SCK: J2.23, U1.19 (GPIO14)
/SCL: J8.3, R6.1, U1.5 (GPIO3), U2.2 (SCK)
/SDA: J8.4, R7.1, U1.4 (GPIO2), U2.4 (SDI)
/SI: J2.19, U1.16 (GPIO12)
/TP_CS: J2.26, U1.20 (GPIO15)
/TP_IRQ: J2.11, U1.12 (GPIO9)
/TP_SO: J2.21, U1.17 (GPIO13)
/TX: J22.2, U1.21 (GPIO16)
/leak_signal: Q2.3 (C), R12.1, R13.1, U1.26 (GPIO20)
GND: C1.2, C2.2, C3.2, C4.2, C5.2, C6.2, C7.2, C8.2, CS1.5 (GND), CS2.5 (GND), D1.1 (K), D2.1 (K), D3.1 (K), D4.1 (K), J1.1, J2.6, J2.9, J2.14, J2.20, J2.25, J3.2, J3.3, J4.2, J4.3, J5.1, J6.2, J7.2, J8.2, J9.2, J10.2, J11.2, J12.1, J13.2, J14.1, J15.1, J16.1, J17.1, J18.2, J19.2, J20.2, J21.2, R3.1, R9.1, R12.2, U1.3 (GND), U1.8 (GND), U1.13 (GND), U1.18 (GND), U1.23 (GND), U1.28 (GND), U1.33 (AGND), U1.38 (GND), U1.42 (GND), U2.3 (VSS), U2.5 (SDO), U2.8 (VSS), U2.9 (VSS), U3.3 (GND), U4.2 (GND)
unnamed: C1.1, CS1.8 (FILTER)
unnamed: C8.1, CS2.8 (FILTER)
unnamed: D1.2 (A), R13.2
unnamed: D2.2 (A), R17.1
unnamed: D3.2 (A), R18.1
unnamed: D4.2 (A), R19.1
unnamed: J1.2, Q1.1 (S_1), Q1.2 (S_2), Q1.3 (S_3), R4.1
unnamed: J13.1, Q3.1 (S_1), Q3.2 (S_2), Q3.3 (S_3), R2.1
unnamed: J16.2, R5.2
unnamed: J17.2, R14.2
unnamed: Q1.4 (G), R4.2, R5.1
unnamed: Q2.1 (B), R10.2, R11.1
unnamed: Q2.2 (E), R11.2
unnamed: Q3.4 (G), R2.2, R14.1

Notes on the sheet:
Hard kill
CURRENT SENSOR
Voltage sensor
Pressure Sensor
LEAK SENSOR

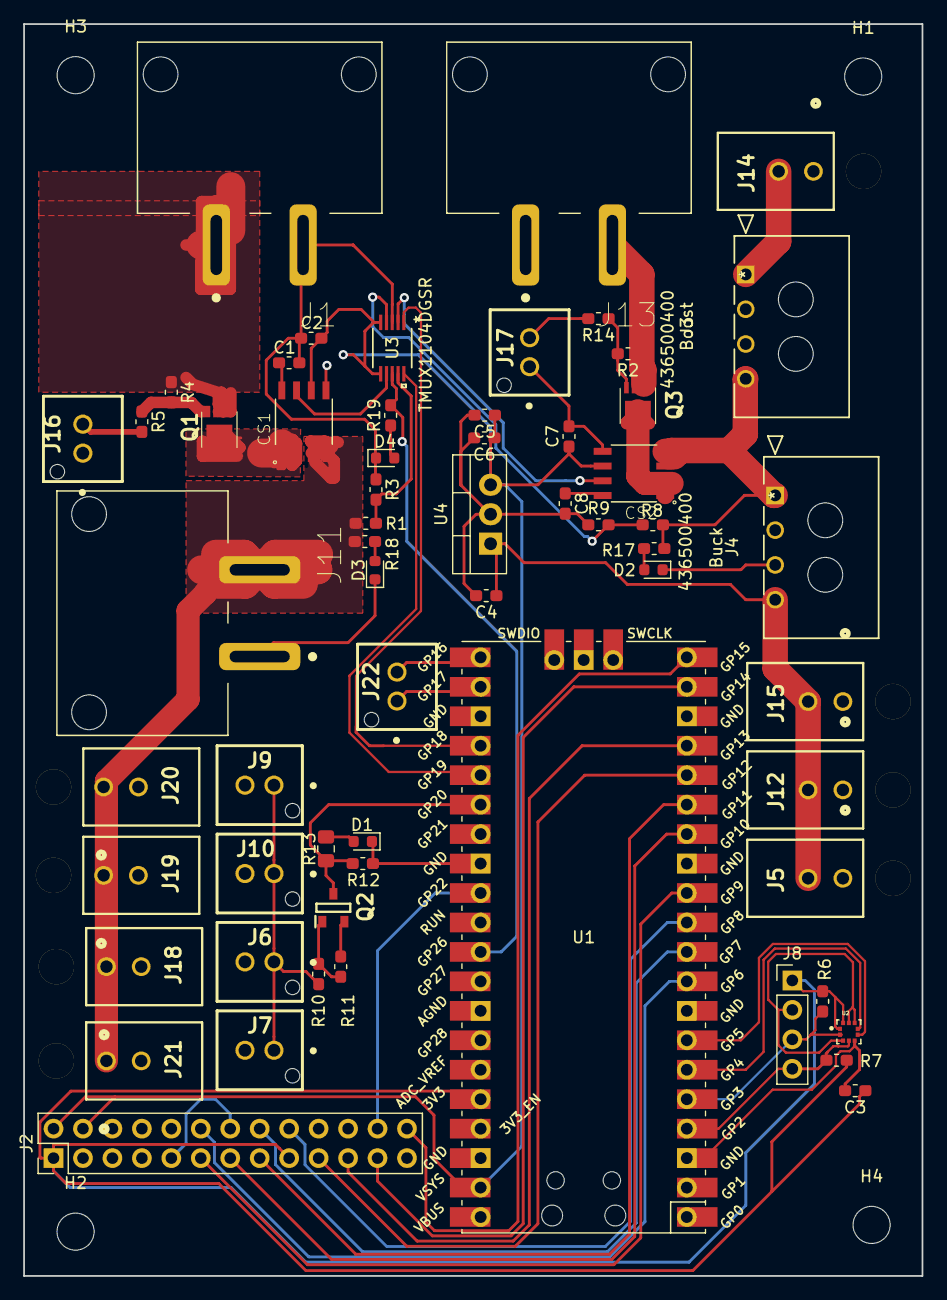
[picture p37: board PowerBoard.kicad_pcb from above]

Board: 2 copper layers, 77.5 x 107.9 mm, 64 parts (0 on the bottom side), 49 nets.

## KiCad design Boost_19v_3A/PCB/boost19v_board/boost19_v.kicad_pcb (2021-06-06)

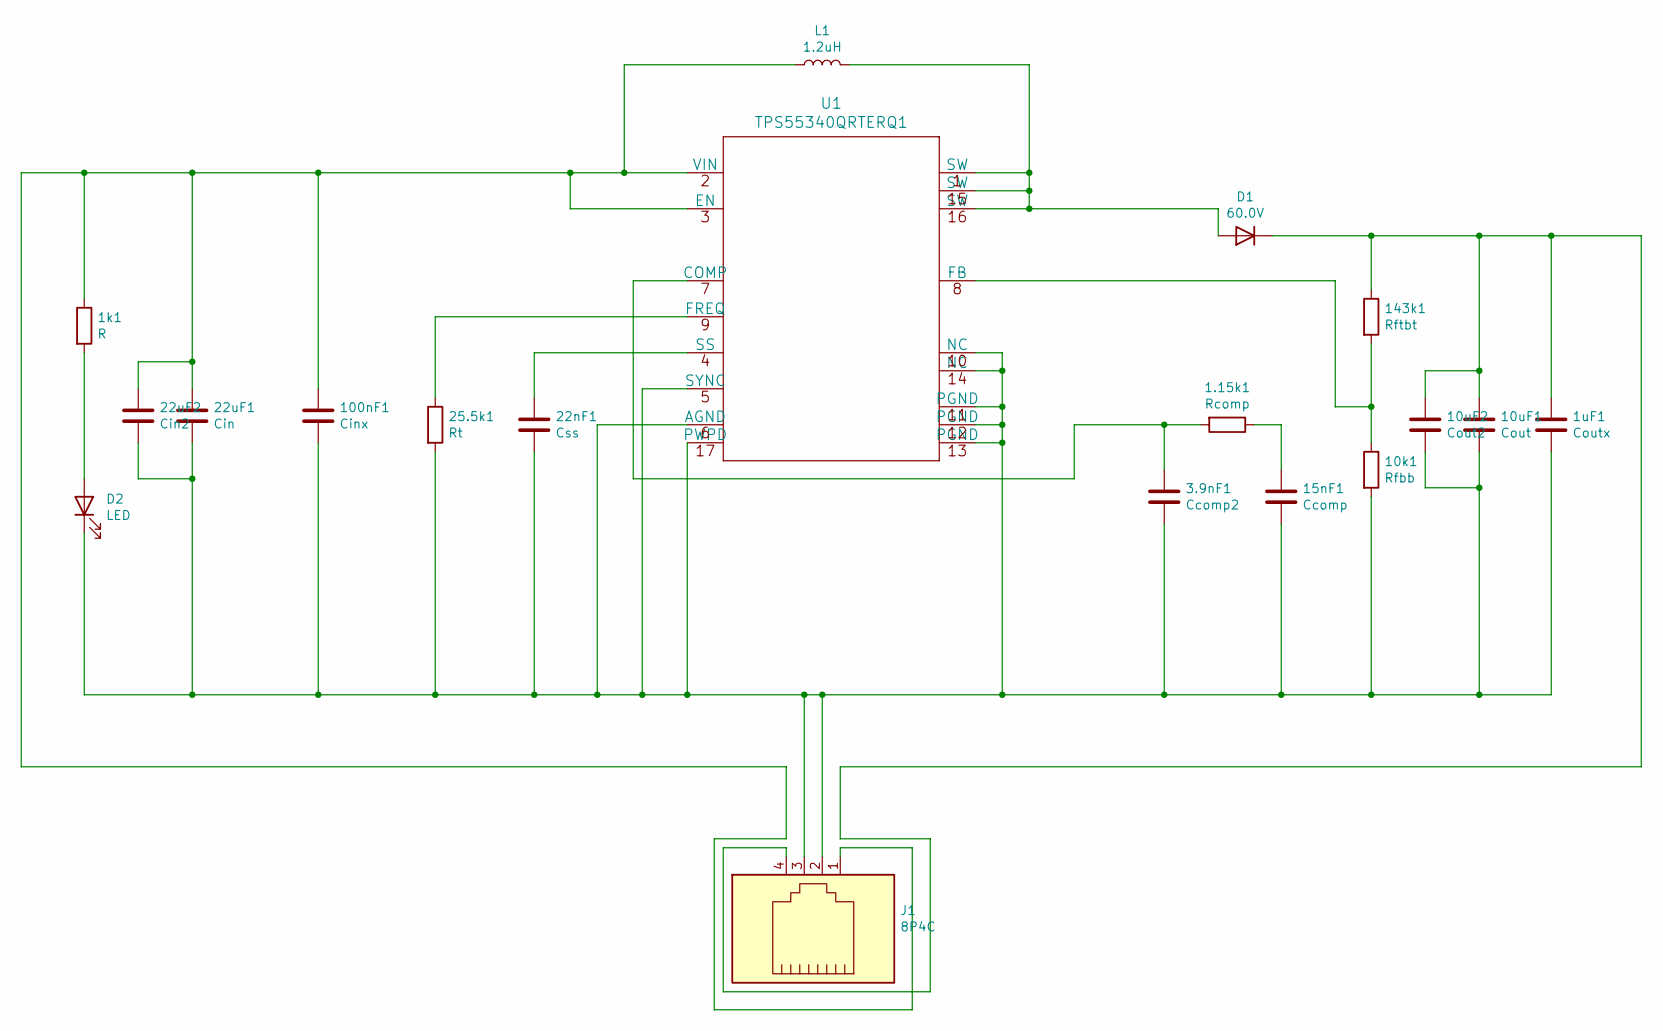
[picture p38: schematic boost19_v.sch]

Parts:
1.15k1: Rcomp; R_0402_1005Metric_Pad0.72x0.64mm_HandSolder
1k1: R; R_1206_3216Metric_Pad1.30x1.75mm_HandSolder
1uF1: Coutx; C_0805_2012Metric_Pad1.18x1.45mm_HandSolder
3.9nF1: Ccomp2; C_0201_0603Metric_Pad0.64x0.40mm_HandSolder
10k1: Rfbb; R_0201_0603Metric_Pad0.64x0.40mm_HandSolder
10uF1: Cout; C_1210_3225Metric_Pad1.33x2.70mm_HandSolder
10uF2: Cout2; C_1210_3225Metric_Pad1.33x2.70mm_HandSolder
15nF1: Ccomp; C_0201_0603Metric_Pad0.64x0.40mm_HandSolder
22nF1: Css; C_0402_1005Metric_Pad0.74x0.62mm_HandSolder
22uF1: Cin; C_0805_2012Metric_Pad1.18x1.45mm_HandSolder
22uF2: Cin2; C_0805_2012Metric_Pad1.18x1.45mm_HandSolder
25.5k1: Rt; R_0402_1005Metric_Pad0.72x0.64mm_HandSolder
100nF1: Cinx; C_0402_1005Metric_Pad0.74x0.62mm_HandSolder
143k1: Rftbt; R_0402_1005Metric_Pad0.72x0.64mm_HandSolder
D1: 60.0V; D_PowerDI-5
D2: LED; LED_1206_3216Metric_Pad1.42x1.75mm_HandSolder
J1: 8P4C; 436500400
L1: 1.2uH; L_Wuerth_MAPI-4030
U1: TPS55340QRTERQ1; TPS55340QRTERQ1_002

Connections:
unnamed: 1.15k1.1, 15nF1.1
unnamed: 1.15k1.2, 3.9nF1.1, U1.7 (COMP)
unnamed: 1k1.2, D2.2 (A)
unnamed: 10k1.1, 143k1.2, U1.8 (FB)
unnamed: 1uF1.1, 10uF1.1, 10uF2.1, 143k1.1, D1.1 (K), J1.4
unnamed: 22nF1.1, U1.4 (SS)
unnamed: 25.5k1.1, U1.9 (FREQ)
unnamed: 1k1.1, 22uF1.1, 22uF2.1, 100nF1.1, J1.1, L1.1, U1.2 (VIN), U1.3 (EN)
unnamed: 1uF1.2, 3.9nF1.2, 10k1.2, 10uF1.2, 10uF2.2, 15nF1.2, 22nF1.2, 22uF1.2, 22uF2.2, 25.5k1.2, 100nF1.2, D2.1 (K), J1.2, J1.3, U1.5 (SYNC), U1.6 (AGND), U1.10 (NC), U1.11 (PGND), U1.12 (PGND), U1.13 (PGND), U1.14 (NC), U1.17 (PWPD)
unnamed: D1.2 (A), L1.2, U1.1 (SW), U1.15 (SW), U1.16 (SW)

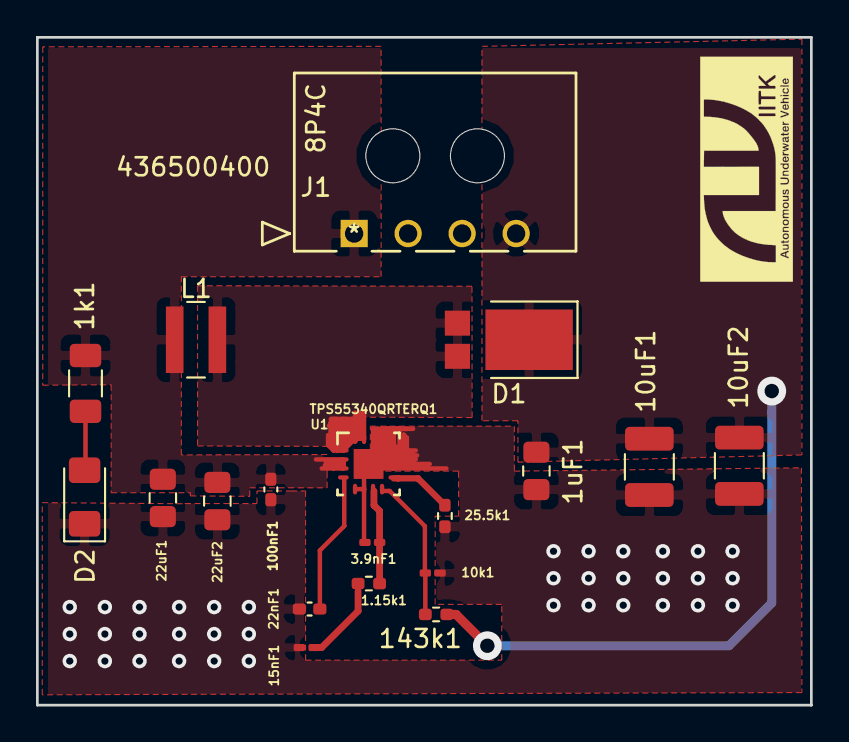
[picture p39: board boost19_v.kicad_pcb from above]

Board: 2 copper layers, 43.0 x 37.1 mm, 19 parts (0 on the bottom side), 10 nets.

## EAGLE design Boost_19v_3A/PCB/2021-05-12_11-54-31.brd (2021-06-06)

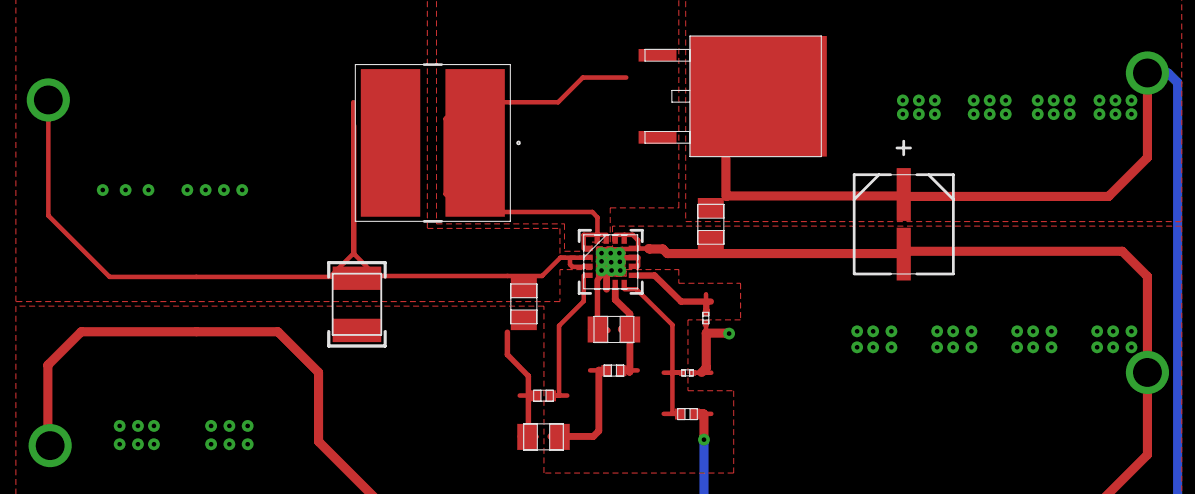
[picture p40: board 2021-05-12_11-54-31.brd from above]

Board: 4 copper layers, 18 parts (0 on the bottom side), 10 nets.

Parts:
Ccomp, Ccomp2: 0805
Cin: 1210
Cinx: 0805
Cout: CAPSMT_62_E61
Coutx: 0805
Css: 0402
D1: DPAK
GND, GND1: TP-5012
L1: VLP8040
Rcomp: 0402
Rfbb: 0201
Rfbt: 0402
Rt: 0201
U1: S-PWQFN-N16
Vin: TP-5012
Vout: TP-5012

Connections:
0: Ccomp.2, Ccomp2.1, Cin.2, Cinx.2, Cout.2, Coutx.2, Css.2, GND.1, GND1.1, Rfbb.2, Rt.2, U1.5, U1.6, U1.11, U1.12, U1.13, U1.17
1: Cin.1, Cinx.1, L1.1, U1.2, U1.3, Vin.1
2: Css.1, U1.4
3: Rfbb.1, Rfbt.2, U1.8
4: Ccomp2.2, Rcomp.2, U1.7
5: D1.1, D1.3, L1.2, U1.1, U1.15, U1.16
6: Rt.1, U1.9
8: Ccomp.1, Rcomp.1
9: Cout.1, Coutx.1, D1.2, Rfbt.1, Vout.1
S$10netdata: U1.10, U1.14

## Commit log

2020-04-30 made branch Buck_5-12v
2020-09-05 organising branch Atmega2560
    [MicrocontrollerPcb.kicad_pcb, MicrocontrollerPcb.sch]
2020-11-17 New commit altogether, ignore previous
    [MicrocontrollerPcb.kicad_pcb, MicrocontrollerPcb.sch]
2020-11-28 Completed PCB Layout changed Input Connector footprint
    [MicrocontrollerPcb.sch]
2020-12-28 Changed component Inductor->Fuse
    [MicrocontrollerPcb.kicad_pcb, MicrocontrollerPcb.sch]
2020-12-28 schematic completed
    [4ESC_board.kicad_pcb, 4ESC_board.sch]
2020-12-30 PCBlayout, Routing, 3DModels, DONE
    [4ESC_board.sch, ESC_BESC30-R3.STEP, Molex_Microfit_1x5_436500500.stp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]
2021-01-10 Removed Trace error
    [MicrocontrollerPcb.kicad_pcb]
2021-01-17 boost converter schematic
    [test5.sch]
2021-01-28 footprints of boost converter
2021-05-22 new board
    [BMP388.step, IRFZ34PBF (1).stp, LM7805CT_NOPB.step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]
2021-05-24 issues resolved
    [PowerBoard.sch]
2021-05-24 boost 19_V complete board
    [boost19_v.kicad_pcb, boost19_v.sch]
2021-05-25 resistance values added to LED
    [PowerBoard.sch]
2021-05-25 BMP issue resolved
    [PowerBoard.sch]
2021-05-27 boost19v pcb layout updated
    [boost19_v.kicad_pcb, boost19_v.sch]
2021-05-28 boost 19v
    [boost19_v.kicad_pcb, boost19_v.sch]
2021-05-28 .brd file
    [2021-05-12_11-54-31.brd]
2021-06-04 Initiated the PCB layout."
    [PowerBoard.sch]
2021-06-04 Adding buck
    [436500400.stp, CGA4C2C0G1H472J060AA.STEP, CSD17304Q3.STEP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]
2021-06-06 minor fixes, size reduced
    [436500400.stp, boost19_v.kicad_pcb]
2021-06-06 Intermediate PCB layout completed.
    [PowerBoard.kicad_pcb, PowerBoard.sch]
2021-06-07 Power Board completed
    [PowerBoard.kicad_pcb, PowerBoard.sch]
2021-06-08 issue resolved
    [430450200.stl, 436500400.stp, 533750210.stl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]
2021-06-08 Added 3D models
    [430450200.stp, 533750210.stp, PowerBoard.kicad_pcb]
2021-06-09 updated power-board and stp file
    [430450200.stp, 430451000.stp, 533750210.stp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]
2021-06-09 Changed the mosfet simulation
2022-03-16 power-trace plane changed, gerber-BOM generated
    [4ESC_board-B.Cu.gbl, 4ESC_board-B.Mask.gbs, 4ESC_board-B.Paste.gbp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]
2022-03-17 added fuse
    [4ESC_board-B.Cu.gbl, 4ESC_board-B.Mask.gbs, 4ESC_board-B.Paste.gbp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]

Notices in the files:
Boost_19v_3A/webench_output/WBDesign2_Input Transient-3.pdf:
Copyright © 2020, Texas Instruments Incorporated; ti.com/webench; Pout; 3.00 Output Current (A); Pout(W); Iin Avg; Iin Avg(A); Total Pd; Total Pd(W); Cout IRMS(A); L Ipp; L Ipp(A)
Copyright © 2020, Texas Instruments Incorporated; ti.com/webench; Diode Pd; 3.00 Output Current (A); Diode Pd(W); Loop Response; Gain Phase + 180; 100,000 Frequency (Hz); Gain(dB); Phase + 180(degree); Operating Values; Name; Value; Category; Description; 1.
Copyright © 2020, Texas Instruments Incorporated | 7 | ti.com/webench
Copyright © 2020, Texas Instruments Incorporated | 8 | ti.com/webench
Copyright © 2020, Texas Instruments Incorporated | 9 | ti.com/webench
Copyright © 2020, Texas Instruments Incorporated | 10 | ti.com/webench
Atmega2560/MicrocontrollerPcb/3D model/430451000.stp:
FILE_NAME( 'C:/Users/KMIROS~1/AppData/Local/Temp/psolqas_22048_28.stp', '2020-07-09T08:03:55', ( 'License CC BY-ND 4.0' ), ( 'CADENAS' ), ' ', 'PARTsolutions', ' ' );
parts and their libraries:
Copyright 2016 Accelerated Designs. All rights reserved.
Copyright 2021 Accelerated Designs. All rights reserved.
